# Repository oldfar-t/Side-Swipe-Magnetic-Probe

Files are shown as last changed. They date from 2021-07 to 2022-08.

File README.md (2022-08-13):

# Side Swipe v1.5 Magnetic Probe - The $10 Bolt On Magnetic Voron v0.1/v0 Probe Solution!

SideSwipe (https://youtu.be/MGC7AC8e7SE "SideSwipe")

Currently Supported Printers: Voron v0.1/v0 using MiniAfterburner direct drive hotend
# BOM
I tried to design this project around Voron v0 parts so hopefully many of these are spare parts you have lying around.
- 2 - M3x8 BHCS or SHCS Bolts (+2 if using Servo_Mount_M3_Nuts_In_Frame)
- 2 - M3x10 BHCS or SHCS Bolts (-2 if using Servo_Mount_M3_Nuts_In_Frame)
- 2 - M3x40 BHCS for Voron MiniAfterburner Mounting
- 2 - M3 Nuts
- 5 - [6mmx3mm Neodymium Magnets](https://www.amazon.com/gp/product/B077K364Z7/ref=ppx_yo_dt_b_asin_title_o00_s01?ie=UTF8&psc=1)
- 1 - [Omron Mouse Microswitch](https://www.amazon.com/dp/B00HPL57JQ/?coliid=I2L344Q2DNJEAU&colid=WW0P09PQO065&psc=1&ref_=lv_ov_lig_dp_it)
- 1 - [MG90s Hobby Metal Gear Servo Motor](https://www.amazon.com/Maxmoral-Upgraded-Digital-Vehicle-Helicopter/dp/B07NV476P7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)
- 1 - [300mm Servo Extension Cable](https://www.amazon.com/gp/product/B01LA9YDEI/ref=ppx_yo_dt_b_search_asin_title?ie=UTF8&psc=1)
- 1 - [550mm Two conductor wire, I used 24 gauge silicon wire that comes as a strip of 4 strands](https://www.amazon.com/BNTECHGO-Silicone-Ribbon-Flexible-Parallel/dp/B07PMS5KGX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)

# Assembly
1. Print all parts using abs, parts are designed with shrinkage in mind. Supports should not be needed and refer to Print_Settings.txt for recommended settings. Decide whether to print the Servo_Mount or Servo_Mount_M3_Nuts_In_Frame. Servo_Mount does not require and M3 nuts to be added to the frame. Servo_Mount_M3_Nuts_In_Frame does require M3 nuts but will require 2 M3 nuts to be added to the front right vertical 15x15 extrusion. I have included some directions in the Troubleshooting section below with some guidance on adding these 2 M3 nuts if you would like to do so.
2. Insert servo connector through hole located in middle of Servo Mount Part then pull wire through.
3. Slot servo side tab into Servo mount with the output shaft closer to the Servo Mount part (See Image Below).
4. Insert M3x8 bolt into hole located on the end of the Servo Mount Part.
5. Insert 2 M3x8 bolts into the mounting holes below servo.
6. Then take the Arm Part and insert and screw in a M3x8 bolt into the hole located on the end between the two prongs.
7. Next press the Arm Part onto the servo output shaft with the text facing upwards, you can also use the screw included with the servo to tighten the arm on but you will need to remove the arm later to calibrate the arm position.
8. Next trim the middle connection on the microswitch flush with the switch body, leaving the two end connections. You will then insert the switch into the Probe Block Part, pressing the switch in so that the connections push through the holes. This is best to be done with a small vise.
9. Bend the switch connections over using a flathead screwdriver.
10. Now insert three 6x3 magnets into the holes of the Probe Block Part, the magnet on the side of the Probe block can be pressed in flush, and the two magnets on top should be pressed so that they are just below the surface of the Block. This can be done by attaching an extra magnet to each to push the magnets further in. Make sure that these two top magnets are facing the same direction.
11. Test the Probe Block with a multimeter on continuity mode by placing the multimeter probes on the top side magnets. The switch is normally closed you you should hear a beep and the beep should stop when pressing the switch. If the continuity test fails refer to troubleshooting below.
12. Take your 550mm section of 2 conductor wire and crimp a 3 connection jst connector(refer to wiring diagram).
13. On the other end trim one of the conductors about 8mm shorter than the other and then strip 20mm of insulation from both conductors.
14. Insert the stripped conductors into the holes on the back of the Probe Mount Part, pull all stripped wire through(twisting the wire first helps).
15. Tuck the wire into the cable channel along the back of the Probe Mount as seen in the image below.
<p align="center">

</p>
16. Coil the stripped wire and tuck into the magnet holes so that they lay roughly flat against the bottom of the hole.
17. Press two 6x3 magnets into the holes on the bottom of the Probe Mount ensuring that they are both the same direction, and that they are oriented such that the Probe Block attaches to the Probe Mount. These magnets should not be pressed until they are flush. The magnets should both be proud of the surface by about 0.5mm.
18. Attach the Probe Block to the Probe Mount and test continuity at the JST connector end of the wire. The switch should behave normally closed. If the continuity test fails refer to troubleshooting below.

View of Probe Switch             |  View of Coupling Magnets
:-------------------------:|:-------------------------:
  |  

19. Remove the two lower mounting bolts on the face of the MiniAfterburner and using two M3x40 bolts attach the Probe Mount using the now open mounting holes.
22. Before attaching the Side Swipe mechanism to the rail, plug the servo into the mainboard following the wiring diagram and run the SERVO_IN macro. You should then adjust the Arm so that it is in line with the body of the servo. Press the arm into place and attach using screw provided with the servo. Running the SERVO_OUT macro should rotate the servo counterclockwise by 90 degrees.
23. You can then attach the Side Swipe mechanism to the extrusion by first backing the 2 M3x10 screws all the way out and then slide the backet into the extrusion, making sure that the servo wire runs up in the extrusion slot towards the top of the machine and underneath the top horizontal extrusion (It helps to place the machine on its face and remove the right side panel).
24. Before tightening the bracket into place adjust the height of the bracket first so that when the arm is in the extended position, the probe can be picked up properly.
25. The servo wire can be tucked into the bottomside slot of the top horizontal extrusion. You might need to remove the servo wire connector so that you can slide the wires past the rear cover plate into the electronics bay. Reattach the connector and attach the 300mm servo extension or cut and solder the wires so that they can reach the mainboard of the printer.
26. Before reattaching the printer side panel, move the print head so that the Probe Mount can reach the Probe Block when the Arm is in the 90 degree position. Loosen and slide the Side Swipe mechanism until the Probe Block makes contact with the Probe Mount. Keep sliding the Side Swipe until the Arm is level and then tighten the two mounting bolts.
27. You should then wire the servo motor and Probe switch connection according to the wiring diagram.
28. Done! You should be able to run the PROBE_IN and PROBE_OUT macros. You may need to make some adjustments to the macro's positioning depending on your printers exact configuration. This is most easily done by moving the printhead manually and then issuing an M114 command to determine the printhead's position.

Servo Assembly             |  Probe Assembly
:-------------------------:|:-------------------------:
  |  

# Troubleshooting
-If continuity test fails for the Probe_Block the top two magnets can be removed by using the included 1.7mm holes. Using a small philips screw driver or drill bit you can remove the thin walls marked with the small 0.5mm hole printed in place on the v2.5 version of the Probe_Block model. Next use a small flat head screwdriver to push the rest of the way, levering the magnet out gently. Please refer to the images below.

Breaking Thin Wall             |  Inserting Flat Head Driver
:-------------------------:|:-------------------------:
  |  

-If continuity test fails for the Probe_Mount the two magnets can be removed by using the included 1.7mm holes. Using a small philips screw driver or drill bit you can remove the thin walls marked with the small 0.5mm hole printed in place on the v7.2 version of the Probe_Mount model. Next use a small flat head screwdriver to push the rest of the way, pushing the magnet out gently. Please refer to the images below.

<p align="center">

</p>

-If using Servo_Mount_M3_Nuts_In_Frame and you have not already added 2 M3 nuts to the front right vertical 15x15 extrusion you will need to do so. This can be done by detensioning the belts, loosening the bolt passing through the front right idler, loosening the three M3 bolts attaching the vertical extrusion to the top and two bottom horizontal extrusions. You can then slide the extrusion down and insert the two M3 nuts into the top of the slot facing the rear of the printer. Slide the extrusion back into place and retighten the M3 bolts ensuring that the extrusions are perpendicular to each other, then screw the top idler bolt back into place.

# Completed Assembly
v1 5 Release Render
v1 5 thumbnail
Render3

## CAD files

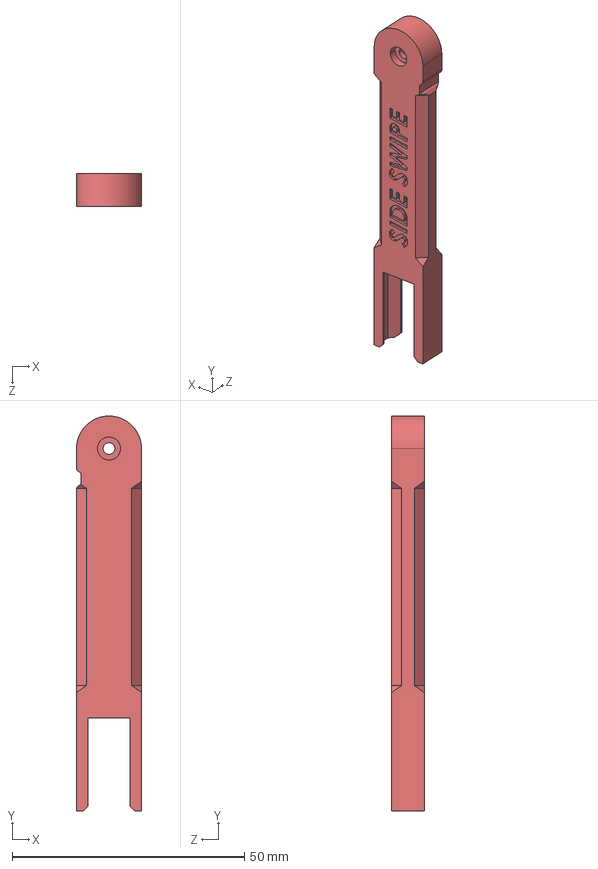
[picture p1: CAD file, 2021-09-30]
Side_Swipe_STEPs/Arm_v2.4.STEP
14.0 x 85.0 x 7.00 mm

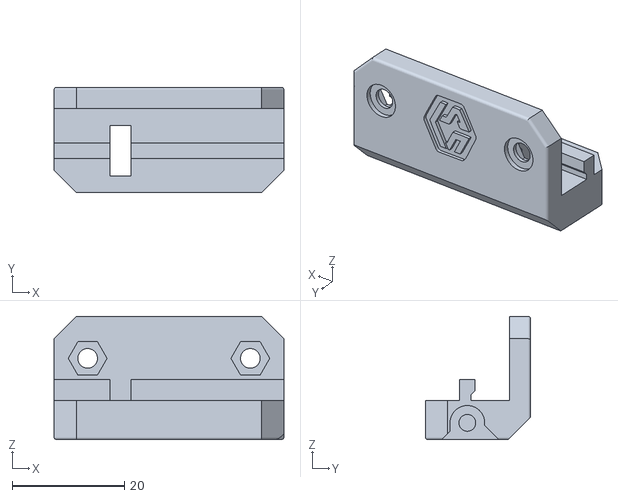
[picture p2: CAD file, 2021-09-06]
Side_Swipe_STLs/Servo_Mount_v7.2.STL
41.0 x 18.8 x 22.0

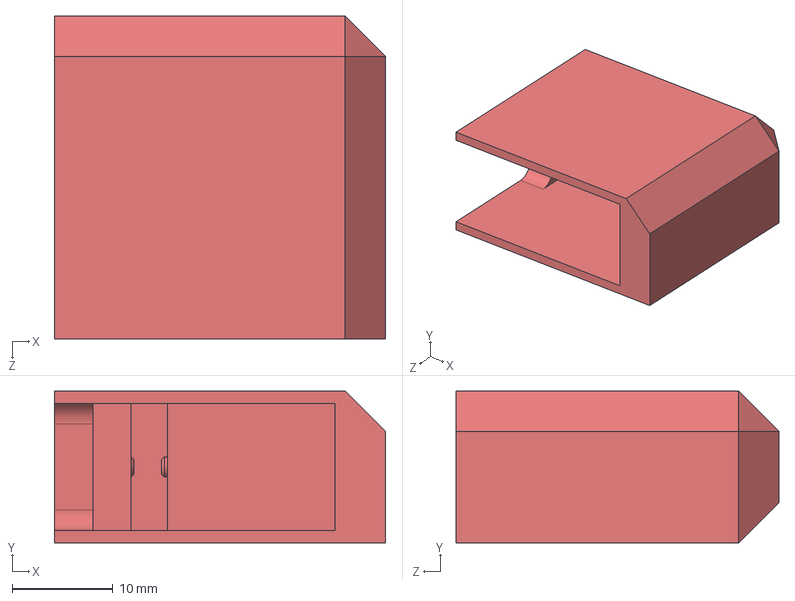
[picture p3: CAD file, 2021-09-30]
Side_Swipe_STEPs/Servo_Case_v2.4.STEP
32.8 x 15.1 x 32.0 mm

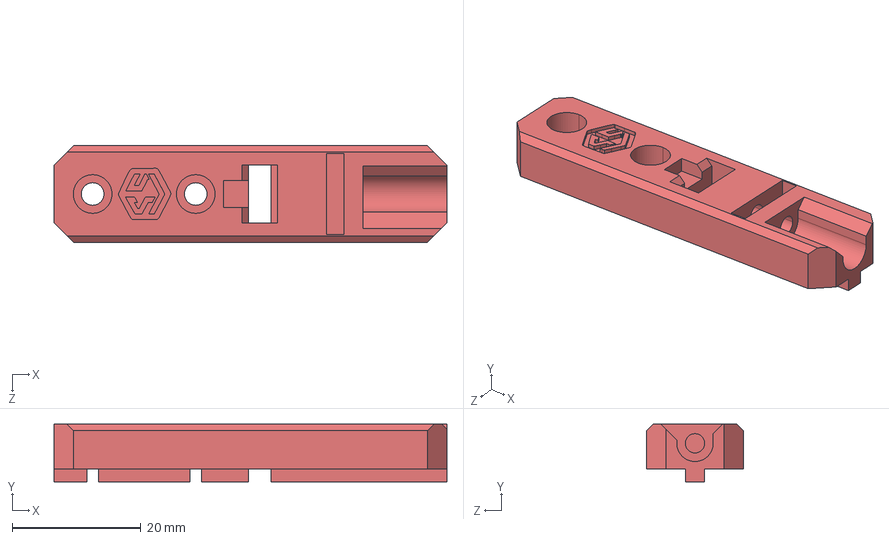
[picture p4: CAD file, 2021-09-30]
Side_Swipe_STEPs/Servo_Mount_M3_Nuts_In_Frame_v1.STEP
61.0 x 9.00 x 15.0 mm

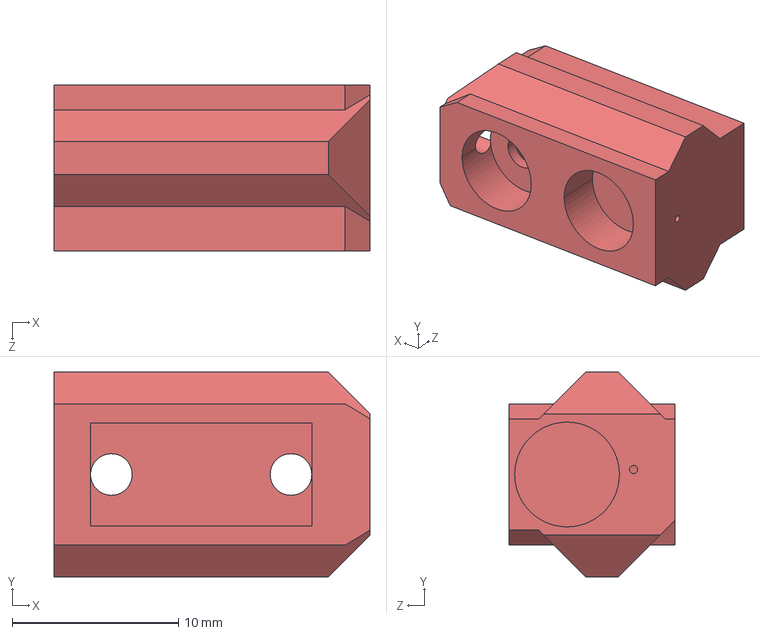
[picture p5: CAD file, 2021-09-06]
Side_Swipe_STEPs/Probe_Block_v2.5.STEP
19.0 x 12.3 x 10.0 mm

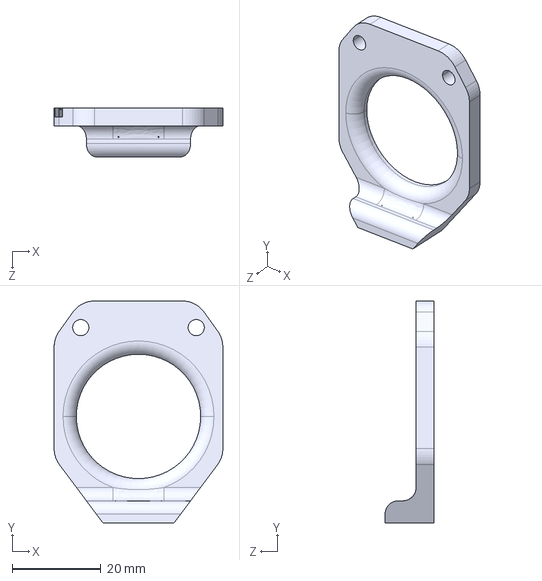
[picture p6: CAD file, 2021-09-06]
Side_Swipe_STEPs/Probe_Mount_v2.2.STEP
38.0 x 50.0 x 11.0 mm

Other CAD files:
Side_Swipe_STEPs/Servo_Mount_v7.1.STEP
Side_Swipe_STLs/Arm_v2.4.STL
Side_Swipe_STLs/Probe_Block_v2.5.STL
Side_Swipe_STLs/Probe_Mount_v2.2.STL
Side_Swipe_STLs/Servo_Case_v2.4.STL
Side_Swipe_STLs/Servo_Mount_M3_Nuts_In_Frame_v1.STL

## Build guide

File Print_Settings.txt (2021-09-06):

Side Swipe Slicer Settings
Recommended Filament Type - ABS, ABS+ - PLA may be possible but parts are designed for ABS shrinkage

0.4mm Nozzle
-Infill - Gyroid 40%
-Walls - 3
-Layer Height - 0.2 recommended, 0.3 possible at reduced quality
-Top/Bottom Layers - 3

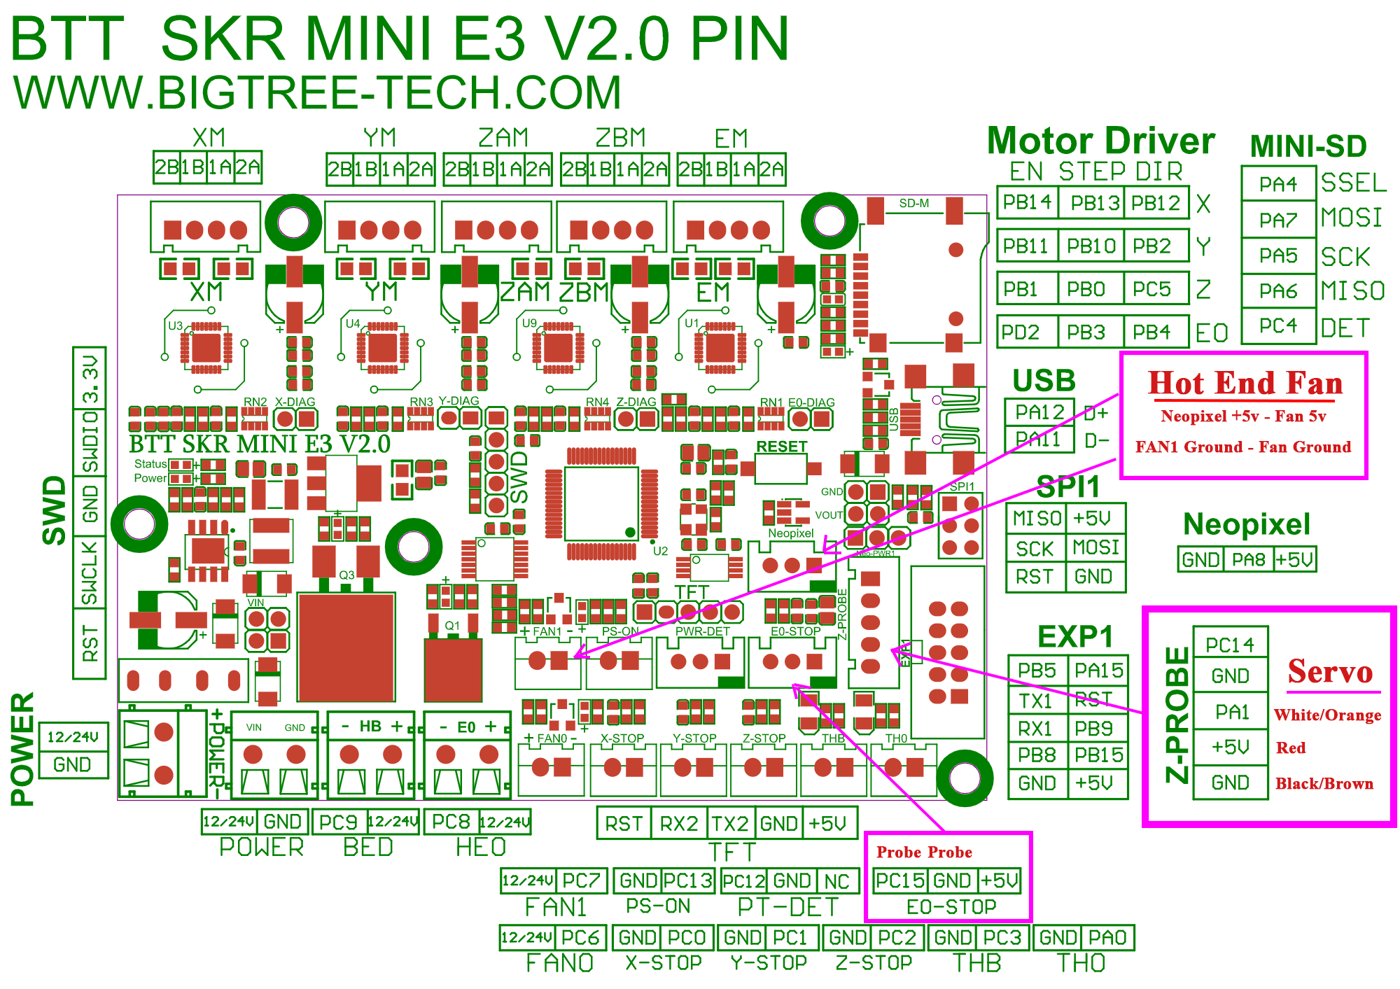
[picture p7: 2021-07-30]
Side Swipe Wiring Diagram - SKR Mini E3 V2.png

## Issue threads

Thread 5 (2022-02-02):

Use of PC15 instead of PC14

daschu117, 2022-02-02:
Why not use PC14 that's part of the z-probe header for the microswitch? I suppose that I can see it being simpler to make independent JST headers instead of awkwardly merging two cables into one header or encouraging the use of non-polarized dupont plugs for the servo connection.

But it should be equivalent and tidier, right? Especially if someone was interested in a filament runout sensor and this mod.

Anyway, thanks for making this available!

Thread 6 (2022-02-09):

MG90S not fitting in case

harlock3, 2022-02-09:
Hi,
Discovered that some MG90S have different dimensions when it comes to the "lip".  Many of them have the lip higher up and won't fit.
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 May want to look at making case version for both (if that's doable).

Rad3d21, 2022-03-09:
ran into this issue too. Edited the files to move the hole.

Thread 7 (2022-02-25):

450mm is not long enough on a LDO 0.1

Znubbis, 2022-02-25:
450mm for the cable from the toolhead is not long enough on a LDO v0.1 kit from LDO, make that 550mm to be sure.

Thank you for a nice design!

oldfar-t, 2022-08-13:
Thank you for the suggestion. I've increased the recommended wire length.

Closed 2022-08-13.

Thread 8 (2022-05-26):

Movement path blocked by light bar

MichaelMichaelMichaelMichaelMichael, 2022-05-26:
Hi, I have a problem using the otherwise fantastic side-swipe-magnetic-probe: it's movement path is being blocked by the lighting which I have mounted like shown in the pictures. It's not possible to mount the servo lower because of the required operation height.
Do you have any advice other than removing the light?

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
Thank you in advance

oldfar-t, 2022-05-27:
Hi! That is an interesting problem since you can't just move the assembly further down. Do you have lighting on both sides of the frame? You could mirror the printed parts and mount the side swipe mechanism to the left side of the frame.

MichaelMichaelMichaelMichaelMichael, 2022-05-30:
Well, the light bars are on both sides, but meanwhile I've changed my mind and I will put my light bars higher. Not all mods can necessarily be combined with each other. Thank you nonetheless for having had a second set of eyes on that.

Closed 2022-05-30.

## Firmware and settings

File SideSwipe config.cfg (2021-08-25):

[stepper_z]
endstop_pin: probe:z_virtual_endstop #default PC2 for home with Z endstop, Use "probe:z_virtual_endstop" if you want to home with probe

[servo SideSwipe]
pin: PA1 #Probe Connection on SKR mini E3 V2
initial_angle: 0
maximum_servo_angle = 180
minimum_pulse_width = 0.0005
maximum_pulse_width = 0.0024

[probe]
pin: ^PC15 #E0-Stop Connection on SKR mini E3 V2
z_offset: 2.329 #Measure per your specific setup
x_offset: -1
y_offset: -28
speed: 3.0
samples: 2
samples_tolerance_retries: 6

[bed_mesh]
horizontal_move_z: 5
speed: 120
mesh_min: 4,2
mesh_max: 109, 89
probe_count: 3,3
#algorithm: bicubic
relative_reference_index: 4 #Varies based on probe count for 3x3 = 4, for 5x5 = 12

[homing_override] #Use this homing override section only if using probe to home Z (See above [stepper_z])
set_position_z: 5
gcode:
    G1 Z10 #Move bed down 10
    G28 X0 Y0 #Home x y
    G1 X60 Y80 F4000 #Move to center of bed
    PROBE_OUT #Deploy Probe
    G28 Z0 #Home z with probe
    G1 Z10 #Move bed down 10
    PROBE_IN #Retract Probe

[gcode_macro PRINT_START]
#   Use PRINT_START for the slicer starting script - please customize for your slicer of choice
gcode:
    G28
    AUTO_BED_MESH
    BED_MESH_PROFILE LOAD=default
    G1 F8000
    G1 X40 Y11 Z5 F3000
    G92 E0
    G0 Z0.5
    G1 X60 Y11 E7 F200
    G92 E0
    G1 X80 Y11 F5000

[gcode_macro SERVO_OUT] #Debug Deploy Arm
gcode:
    SET_SERVO SERVO=SideSwipe ANGLE=90

[gcode_macro SERVO_IN] #Debug Retract Arm
gcode:
    SET_SERVO SERVO=SideSwipe ANGLE=0
    SET_SERVO SERVO=SideSwipe WIDTH=0

[gcode_macro PROBE_OUT]
gcode:
    G1 X60 Y60 Z10 F4000
    SET_SERVO SERVO=SideSwipe ANGLE=90
    G1 X77 Y36 F4000
    G1 X98 Y36 F1000
    G4 P300
    G1 X61 Y36 F4000
    G4 P300
    SET_SERVO SERVO=SideSwipe ANGLE=0
    SET_SERVO SERVO=SideSwipe WIDTH=0
    G1 X60 Y60 F4000
    G4 P300

[gcode_macro PROBE_IN]
gcode:
    G1 Z10
    G1 X61 Y50 F4000
    SET_SERVO SERVO=SideSwipe ANGLE=90
    G1 X71 Y36 F4000
    G1 X98 Y36 F1000
    G4 P300
    G1 X111 Y36 F2000
    G4 P300
    G1 X111 Y48 F4000
    G1 X60 Y60 F4000
    SET_SERVO SERVO=SideSwipe ANGLE=0
    SET_SERVO SERVO=SideSwipe WIDTH=0
    G4 P300

[gcode_macro AUTO_BED_MESH]
gcode:
    PROBE_OUT
    BED_MESH_CALIBRATE
    PROBE_IN

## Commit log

2021-08-25 Update SideSwipe config.cfg
    -Added samples_tolerance_retries: 6 in the case of probe tolerance error.
    -Added SET_SERVO SERVO=SideSwipe WIDTH=0 to macros which puts servo to sleep when not in use.
    [SideSwipe config.cfg]
2021-08-26 v1.5 STLs Added
    [Arm_v2.3.STL, Probe_Block_v2.4.STL, Probe_Mount_v2.1.STL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]
2021-09-06 New Probe Mount v7.2 and Probe Block v2.5
    -Probe_Mount and Probe_Block now have holes included to push the press fit magnets out in the case of a mistake in wiring.
    -All part now have been oriented for proper print orientation.
    [Arm_v2.3.STL, Probe_Block_v2.5.STL, Probe_Mount_v2.2.STL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]
2021-09-30 v1.6 Update
    Files Updated: Arm_v2.4, Servo_Case_v2.4, Servo_Mount_M3_Nuts_In_Frame_v1
    [Arm_v2.3.STEP, Arm_v2.3.STL, Arm_v2.4.STEP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]
2021-09-30 Update README.md
    Add instructions for new Servo_Mount_M3_Nuts_In_Frame installation
2022-08-13 Update README.md
    Increased length of the 2 conductor probe wire from 450mm to 550mm.
